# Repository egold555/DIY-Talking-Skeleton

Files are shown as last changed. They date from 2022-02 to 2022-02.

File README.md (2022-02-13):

# Modifying Home Depot skeleton

Purchase the "Home Accents Holiday 5 ft. Poseable Skeleton with LED Illumination". Might be available on web site in a set of 6.

Here's how to modify the skeleton and add the servo parts.

## Unscrew screws on the head.

Remove 6 screws from the head. **Save these screws for reassembly!**

Unscrew the screws holding the head to the spine and remove the head. 
These screws will not be needed again.

## Modify battery case

Remove batteries.

Remove Try Me button.

Cut the wires to the LEDs as close as possible to the battery case.

Remove the power switch.

Dremel out the power switch hole so that CAT 5 cable can fit through.

Rescrew battery case screws on.

# Mounting the neck servo

## Modifying Neck

With Dremel, cut off the neck part attached to the head.

With Dremel, cut off one level of neck part attached to the body. There should still be at 
least an inch of hollow tube above the large hole through the neck.

With Dremel sanding tool, clean out the inside of the neck just below the hole.

## Inserting neck servo mount.

Insider the neck servo mount flush down with the battery case back. Sand that flat with the
Dremel if needed. Mark hole positions with the neck mount in place, remove the mount, and use
Dremel to put holes in battery case with 5/64 inch drill bit. 

Insert the mount and screw down with two 1/2 inch #4 sheet metal screws.

## Attach plastic cylinder to servo

Using four very small self-tapping screws (M1.7/5), attach the black plastic cylinder to a round servo
attachment.

Using an Arduino, center the servo at the 90 degree position. At this position the skull should
face forward. 

Attach the servo attachment/cylinder combo to the servo using the main central screw, assuring that
the screw hole is correctly oriented so the skull will face forward when attached.

## Place servo in the mount

Slide the servo into the mount all the way, then attach the top piece using two 1/2 inch #4 sheet metal screws.

# Mounting the jaw servo

## Modifying jaw 

Unscrew the jaw from the white jaw crossbeam. **Save screws!**

Turn the white crossbeam around.

Rescrew the jaw to the white crossbeam so that when the jaw is fully open, the white slot
that sticks out from the crossbeam just touches the inside of the skull in the down position. 
Tighten the screws fairly tight so that it doesn't rotate.

## Inserting Jaw servo mount

Insert the servo mount into the skull. Make sure everything is flat and tight, and the that long 
piece that goes to the back of the head goes between two screw pillars. The crossbeam should be tight
against plastic under the top of the jaw.

Using the Dremel 3/32" drill bit (different than before!) drill two holes through the plastic under the 
jaw into the black plastic of the servo mount.

Screw in two 1/2 inch #4 sheet metal screws to secure the mount.

## Attach servo horn to the servo.

Using four very small (M1.7/5) self-tapping screws, attach the servo horn to the *back* of the round servo attachment.
The servo horn should be closer to the body of the servo than that the servo attached itself when mounted; the
geared hole goes through the hole on the servo horn.

Using an Arduino, center the servo at the 90 degree position. 

Attach the servo horn combination onto the servo with the main central screw. The servo horn should point 
directly away from the servo. This will require trying out 4 different positions on the round plastic connector,
because of the different positions of the gearing.

Careful slide the pin on the servo horn into the slot on the white crossbeam, and then slot the servo into the 
mount. Push all the way down.

Attach the top piece using two 1/2 inch #4 sheet metal screws.

# Solder wires and connector

## 5-wire socket and jaw servo/eyes

Solder 180 Ohm resistor (shorten the ends) to the end of the red eye wire. 

Connect the 5-socket and connector together. Solder **and heat shrink** the following wires to the socket connector (the
part without wires)

* Connector wire color -> Servo/eyes wire
* Green -> Servo Brown wire
* White -> Servo Red wire
* Yellow -> Red eye wire with resistor (use long piece of heat shrink to cover whole resistor)
* Black -> Black eye wire

## CAT-5 to Wires

Get a Cat-5 socket connector. Connect six colored wires as follows, using the "A" wiring standard.

* CAT 5 color -> Wire Color
* Brown -> Green
* Brown Striped -> White
* Green -> Blue
* Orange -> Red
* Blue -> Black
* Blue Stripe -> Yellow

## Neck servo and 5 wire connector

Twist together and solder the Neck Servo Brown wire and Green wire from the 5-wire connector (wires running same way)

Twist together and solder the Neck Servo Red wire and the White wire from the 5-wire connector (wires running same way)

Solder **and heat shrink** wires running from the CAT-5 connector and the wires from the 5-wire connector together as follows:

* Wire color running from Cat-5 connect -> 5-Wire Connector wire color
* Green -> Green connector wire and Neck Servo Brown
* White -> White connector wire and Neck Servo Red
* Red  -> Red connector wire
* Yellow -> Yellow connector wire
* Black -> Black connector wire
* Blue -> Neck Servo Orange

# Assemble

Screw the head together again using the saved screws.

Attach the black plastic neck into the spine, and attach using 1/4 inch, 1 1/4" long bolt and nut. Tighten nut.

# Servo ranges

Jaw servo, in degrees, using Arduino servo library: 102 = full open, 60 = full closed.  Do not go beyond these ranges. 
Getting this right requires that 90 is servo horn directly forward. May require calibrating each head specifically, but
this should get you close.

Neck servo: 90 is forward, 0 and 180 are full to each side.

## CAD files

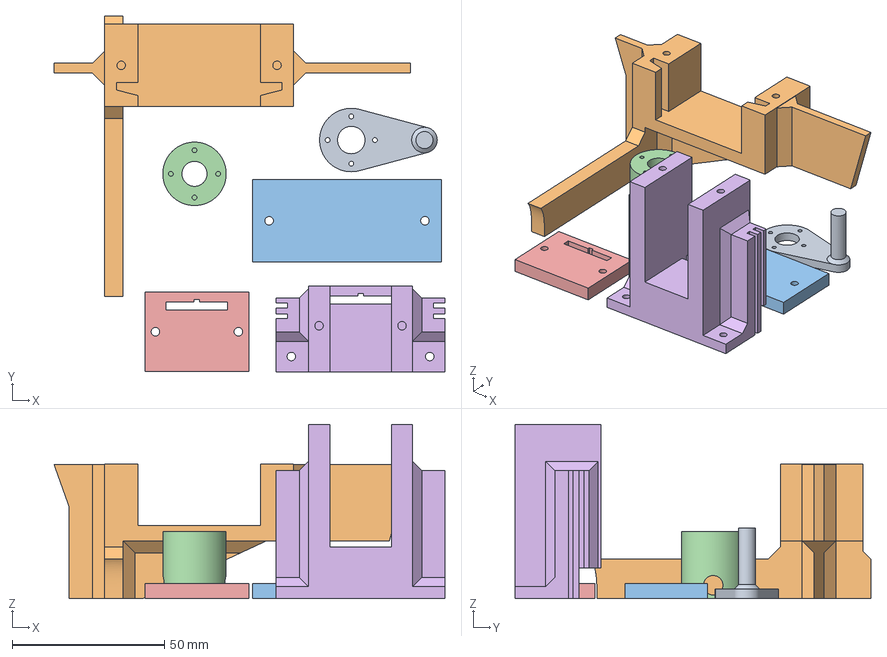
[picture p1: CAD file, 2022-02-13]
3D Models/AllPieces.3mf
128.2 x 116.6 x 57.2 mm
ServoArm.stl
JawServoMount.stl
ServoLid.stl
ServoSide.stl
TopPlate.stl
NeckServoMount.stl

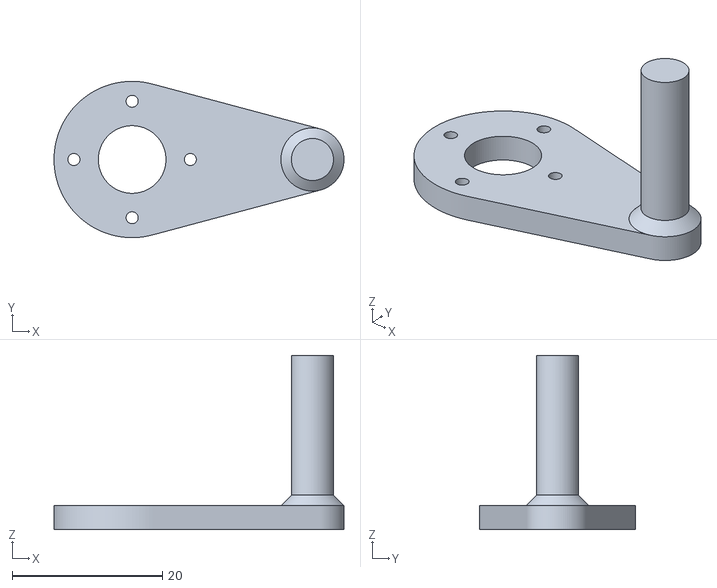
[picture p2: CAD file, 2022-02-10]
3D Models/ServoArm.stl
38.6 x 20.8 x 23.2

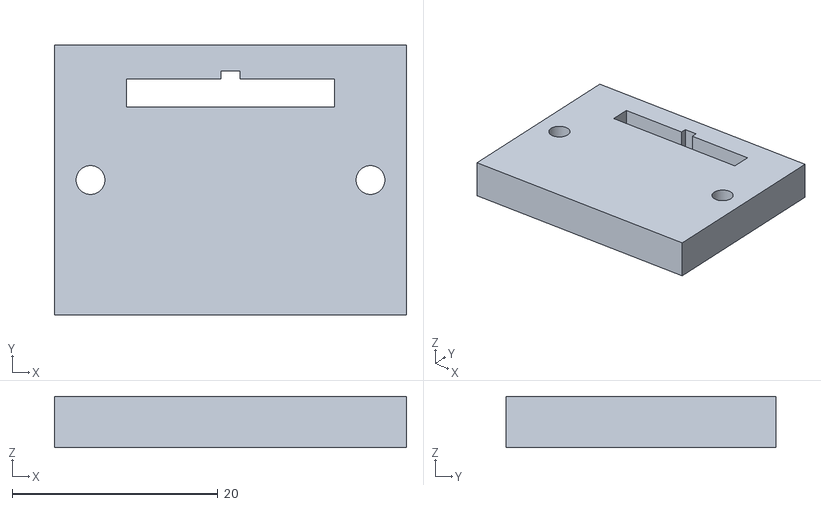
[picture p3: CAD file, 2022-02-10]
3D Models/TopPlate.stl
34.2 x 26.2 x 5.00

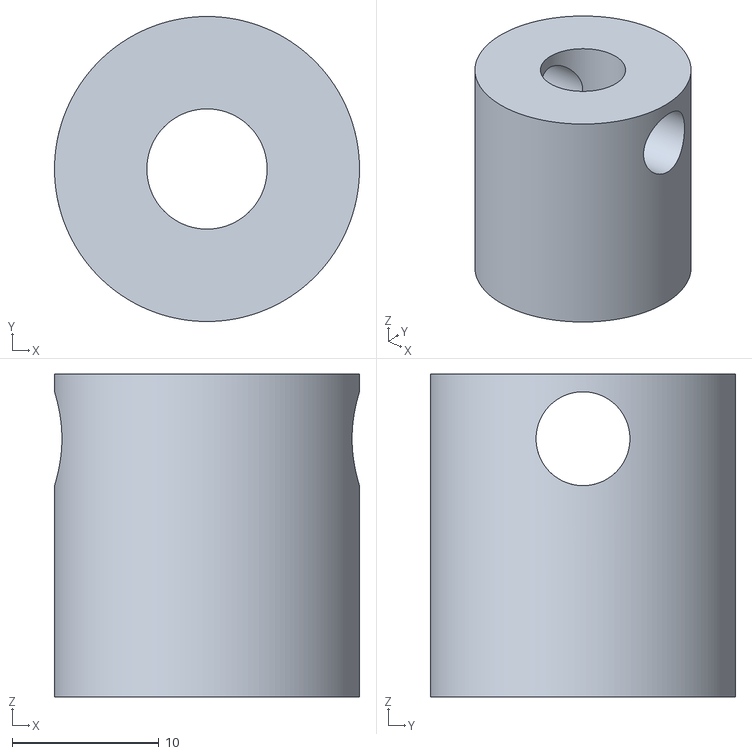
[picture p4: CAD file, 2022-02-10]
3D Models/ServoSide.stl
20.8 x 20.8 x 22.0

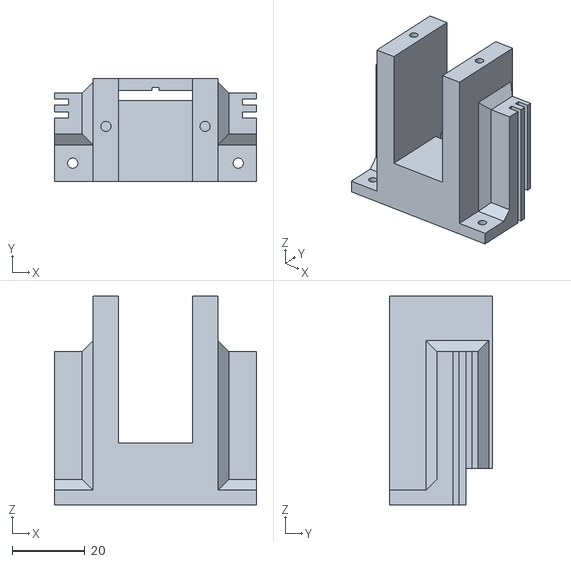
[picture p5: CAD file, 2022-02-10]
3D Models/NeckServoMount.stl
55.4 x 28.2 x 57.2

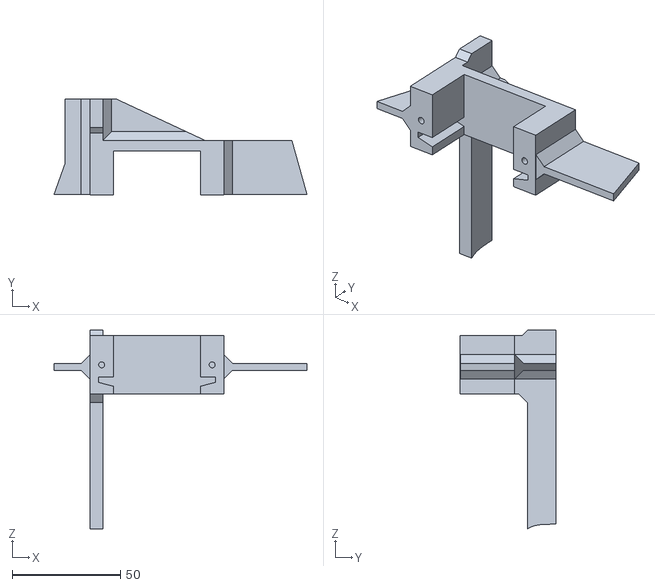
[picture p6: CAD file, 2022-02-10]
3D Models/JawServoMount.stl
117.0 x 44.2 x 92.0

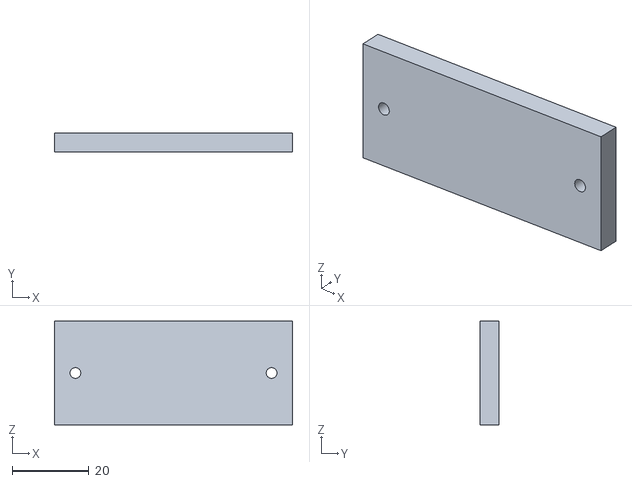
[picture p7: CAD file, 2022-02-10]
3D Models/ServoLid.stl
62.0 x 5.00 x 27.0

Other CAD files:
3D Models/JawServoMount v26.f3d
3D Models/NeckConnector3 v4.f3d
3D Models/NeckServoMount v8.f3d

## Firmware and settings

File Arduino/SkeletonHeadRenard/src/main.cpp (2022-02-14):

#include <Arduino.h>
#include "Renard.h"
#include "Servo.h"
/*
// Renard protocol baud rate.
const int BAUDRATE = 57600;

// Renard channels.
const int TOTAL_CHANNELS = 8;
const int HEAD_CHANNEL = 3;
const int JAW_CHANNEL = 1;
const int EYES_CHANNEL = 2;

// Pins
const int HEAD_SERVO_PIN = 8;
const int JAW_SERVO_PIN = 7;
const int EYES_PWM_PIN = 3;

// Ranges of servos.
const int HEAD_SERVO_LEFT = 0;
const int HEAD_SERVO_RIGHT = 180;
const int HEAD_SERVO_CENTER = 90;
const int JAW_SERVO_CLOSED = 60;
const int JAW_SERVO_OPEN = 102;

Servo headServo;
Servo jawServo;
Renard renard(Serial, TOTAL_CHANNELS);

void setup()
{
  Serial.begin(BAUDRATE);
  headServo.attach(HEAD_SERVO_PIN);
  headServo.write(45);

  jawServo.attach(JAW_SERVO_PIN);
  jawServo.write(JAW_SERVO_OPEN);
  pinMode(EYES_PWM_PIN, OUTPUT);

  analogWrite(EYES_PWM_PIN, 255);
}

void loop()
{

  while (!renard.processInput())
    ;

  int headValue = renard.channelValue(HEAD_CHANNEL);
  if (headValue == 0)
  {
    headServo.write(HEAD_SERVO_CENTER);
  }
  else
  {
    headServo.write(map(headValue, 1, 255, HEAD_SERVO_LEFT, HEAD_SERVO_RIGHT));
  }

  int jawValue = renard.channelValue(JAW_CHANNEL);
  jawServo.write(map(jawValue, 0, 255, JAW_SERVO_CLOSED, JAW_SERVO_OPEN));

  int eyesValue = renard.channelValue(EYES_CHANNEL);
  analogWrite(EYES_PWM_PIN, eyesValue);
}
*/


/*
   Yellow: Pin 9
   Red: +5V
   Brown: GND
*/

//****** NEW BOOTLOADER *******

// Values on the servo that correspond to mouth positions.
const int FULLOPEN = 102;
const int FULLCLOSED = 60;

const int SERVO_MOUTH_PIN = 7;
const int SERVO_HEAD_PIN = 8;
const int EYES_PIN = 3;

Servo servoMouth;
Servo servoHead;
Servo servoEyes;
Renard renard(Serial, 3);

//Reverse left and right on the skeleton, useful for when the parrot is on his right sholder. If so, make it true
const boolean reverseLeftAndRightHead = true;

void setup() {
  // Open serial communications
  Serial.begin(57600);
  pinMode(EYES_PIN, OUTPUT);

  servoMouth.attach(SERVO_MOUTH_PIN);
  servoMouth.write(FULLCLOSED);
  servoHead.attach(SERVO_HEAD_PIN);
  servoHead.write(45);
  analogWrite(EYES_PIN, 255);
}

void loop() {
  // Read renard
  while (!renard.processInput())
    ;

  //Do Mouth
  int channelValueMouth = renard.channelValue(1);
  int posMouth = map(channelValueMouth, 0, 255, FULLCLOSED, FULLOPEN);
  servoMouth.write(posMouth);

  //Do Eyes
  int eyesValue = renard.channelValue(2);
  analogWrite(EYES_PIN, eyesValue);

  

  //Do Head
  int channelValueHead = renard.channelValue(3);
  int headPos = 90;
  if (channelValueHead != 0) {
    if(reverseLeftAndRightHead){
        headPos = map(channelValueHead, 0, 255, 180, 0);
    }
    else {
        headPos = map(channelValueHead, 0, 255, 0, 180);
    }
    
  }
  servoHead.write(headPos);

}

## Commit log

2022-02-13 Add instruction on modifying skeleton
    [AllPieces.3mf]
2022-02-13 Rearrange files
    [AllPieces.3mf, JawServoMount v26.f3d, JawServoMount.stl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]
